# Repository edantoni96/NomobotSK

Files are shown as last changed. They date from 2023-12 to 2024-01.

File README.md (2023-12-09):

# NomobotSK

========== PCB DESIGN FOR NOMOBOT SK ==========

NomobotSK is a educational robot for kids to learn programming and robotics.

## TOP VIEW

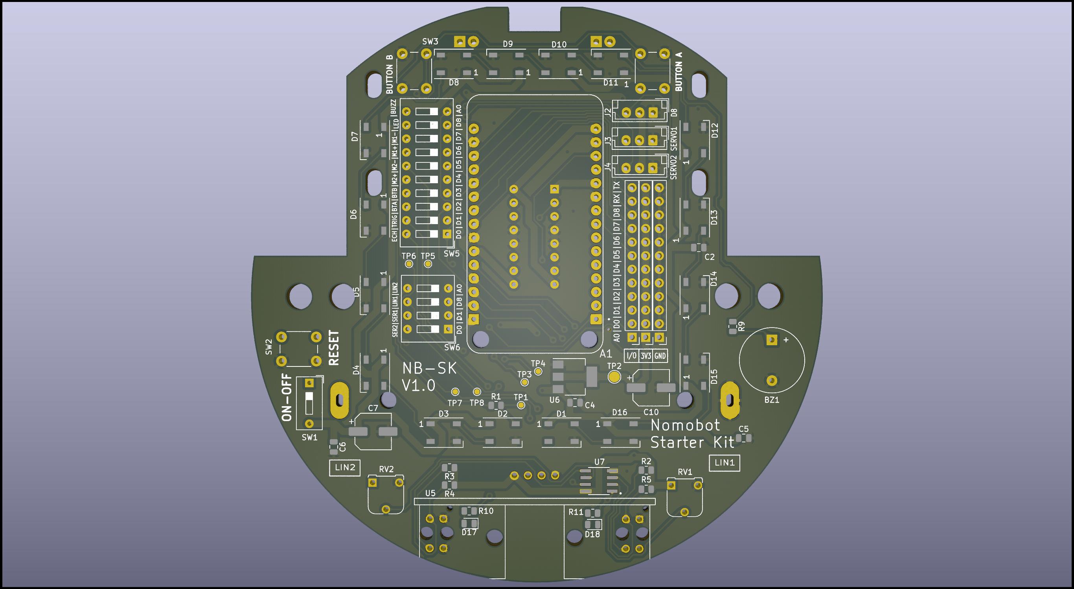
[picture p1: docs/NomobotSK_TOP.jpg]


## BOTTOM VIEW

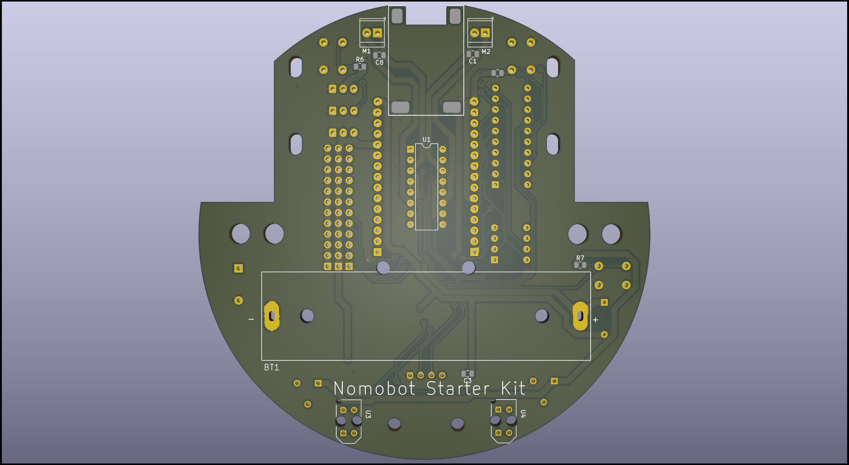
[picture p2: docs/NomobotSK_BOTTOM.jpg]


## SCHEMATIC

[embed](https://github.com/edantoni96/NomobotSK/blob/main/docs/schematic.pdf)

## TESTER

To test the device you can use the under tester/TEST.ino

\***\*KONFIGURASI PIN\*\***

D1; Trig / Servo R
D2; Tombol 2
D3; Tombol 3
D4; DIR2 (-)
D5; DIR2 (+)
D6; DIR1 (-)
D7; DIR1 (+)
D8; LED / Garis L
D0; BUZZ / Garis R

Catatan: Simbol / berarti setiap fungsi perlu diuji atau digunakan secara terpisah.

\***\*Perintah PENGUJIAN\*\***

1. TEST_LED
2. TEST_BUZ
3. TEST_BUTTON
4. TEST_M1
5. TEST_M2
6. TEST_ULRA
7. TEST_LINE

\***\*Instruksi Uji\*\***

1. Buka Test.ino dengan Arduino.
2. compile Test.ino.
3. Hubungkan NodeMCU Anda ke komputer menggunakan kabel USB.
4. Pilih board dan port yang sesuai di Arduino IDE.
5. Unggah kode yang telah dikompilasi ke NodeMCU dengan mengklik tombol "Unggah".
6. Setelah pengunggahan selesai, buka Serial Monitor di Arduino IDE.
7. TEST_LED
   - Nyalakan pin LED
   - Ketik "TEST_LED" di Serial Monitor dan tekan Enter.
   - Pastikan bahwa LED yang terhubung ke pin D8 (Garis L) menyala.
8. TEST_BUZ
   - Nyalakan pin Buzz
   - Ketik "TEST_BUZ" di Serial Monitor dan tekan Enter.
   - Konfirmasikan bahwa buzzer yang terhubung ke pin D0 (Garis R) menghasilkan suara.
9. TEST_BUTTON
   - Nyalakan BTA dan BTB
   - Ketik "TEST_BUTTON" di Serial Monitor dan tekan Enter.
   - Tekan Tombol 2 (terhubung ke pin D2) dan Tombol 3 (terhubung ke pin D3) satu per satu.
   - Amati di Serial Monitor bahwa tekanan tombol yang sesuai terdeteksi.
10. TEST_M1
    - Nyalakan pin M1+ dan M1-
    - Ketik "TEST_M1" di Serial Monitor dan tekan Enter.
    - Pastikan bahwa motor (M1) merespons sesuai dengan sinyal DIR1 (-) dan DIR1 (+) pada pin D6 dan D7.
11. TEST_M2
    - Nyalakan pin M2+ dan M2-
    - Ketik "TEST_M2" di Serial Monitor dan tekan Enter.
    - Pastikan bahwa motor (M2) merespons sesuai dengan sinyal DIR2 (-) dan DIR2 (+) pada pin D4 dan D5.
12. TEST_ULRA
    - Nyalakan pin Echo dan Trig
    - Ketik "TEST_ULRA" di Serial Monitor dan tekan Enter.
    - Jika sensor ultrasonik terhubung, periksa Serial Monitor untuk pembacaan jarak.
13. TEST_LINE
    - Nyalakan pin Garis
    - Ketik "TEST_LINE" di Serial Monitor dan tekan Enter.
    - Amati perilaku sensor garis yang terhubung ke pin D8 (Garis L) dan D0 (Garis R).
    - Pastikan pembacaan sensor tercermin di Serial Monitor.

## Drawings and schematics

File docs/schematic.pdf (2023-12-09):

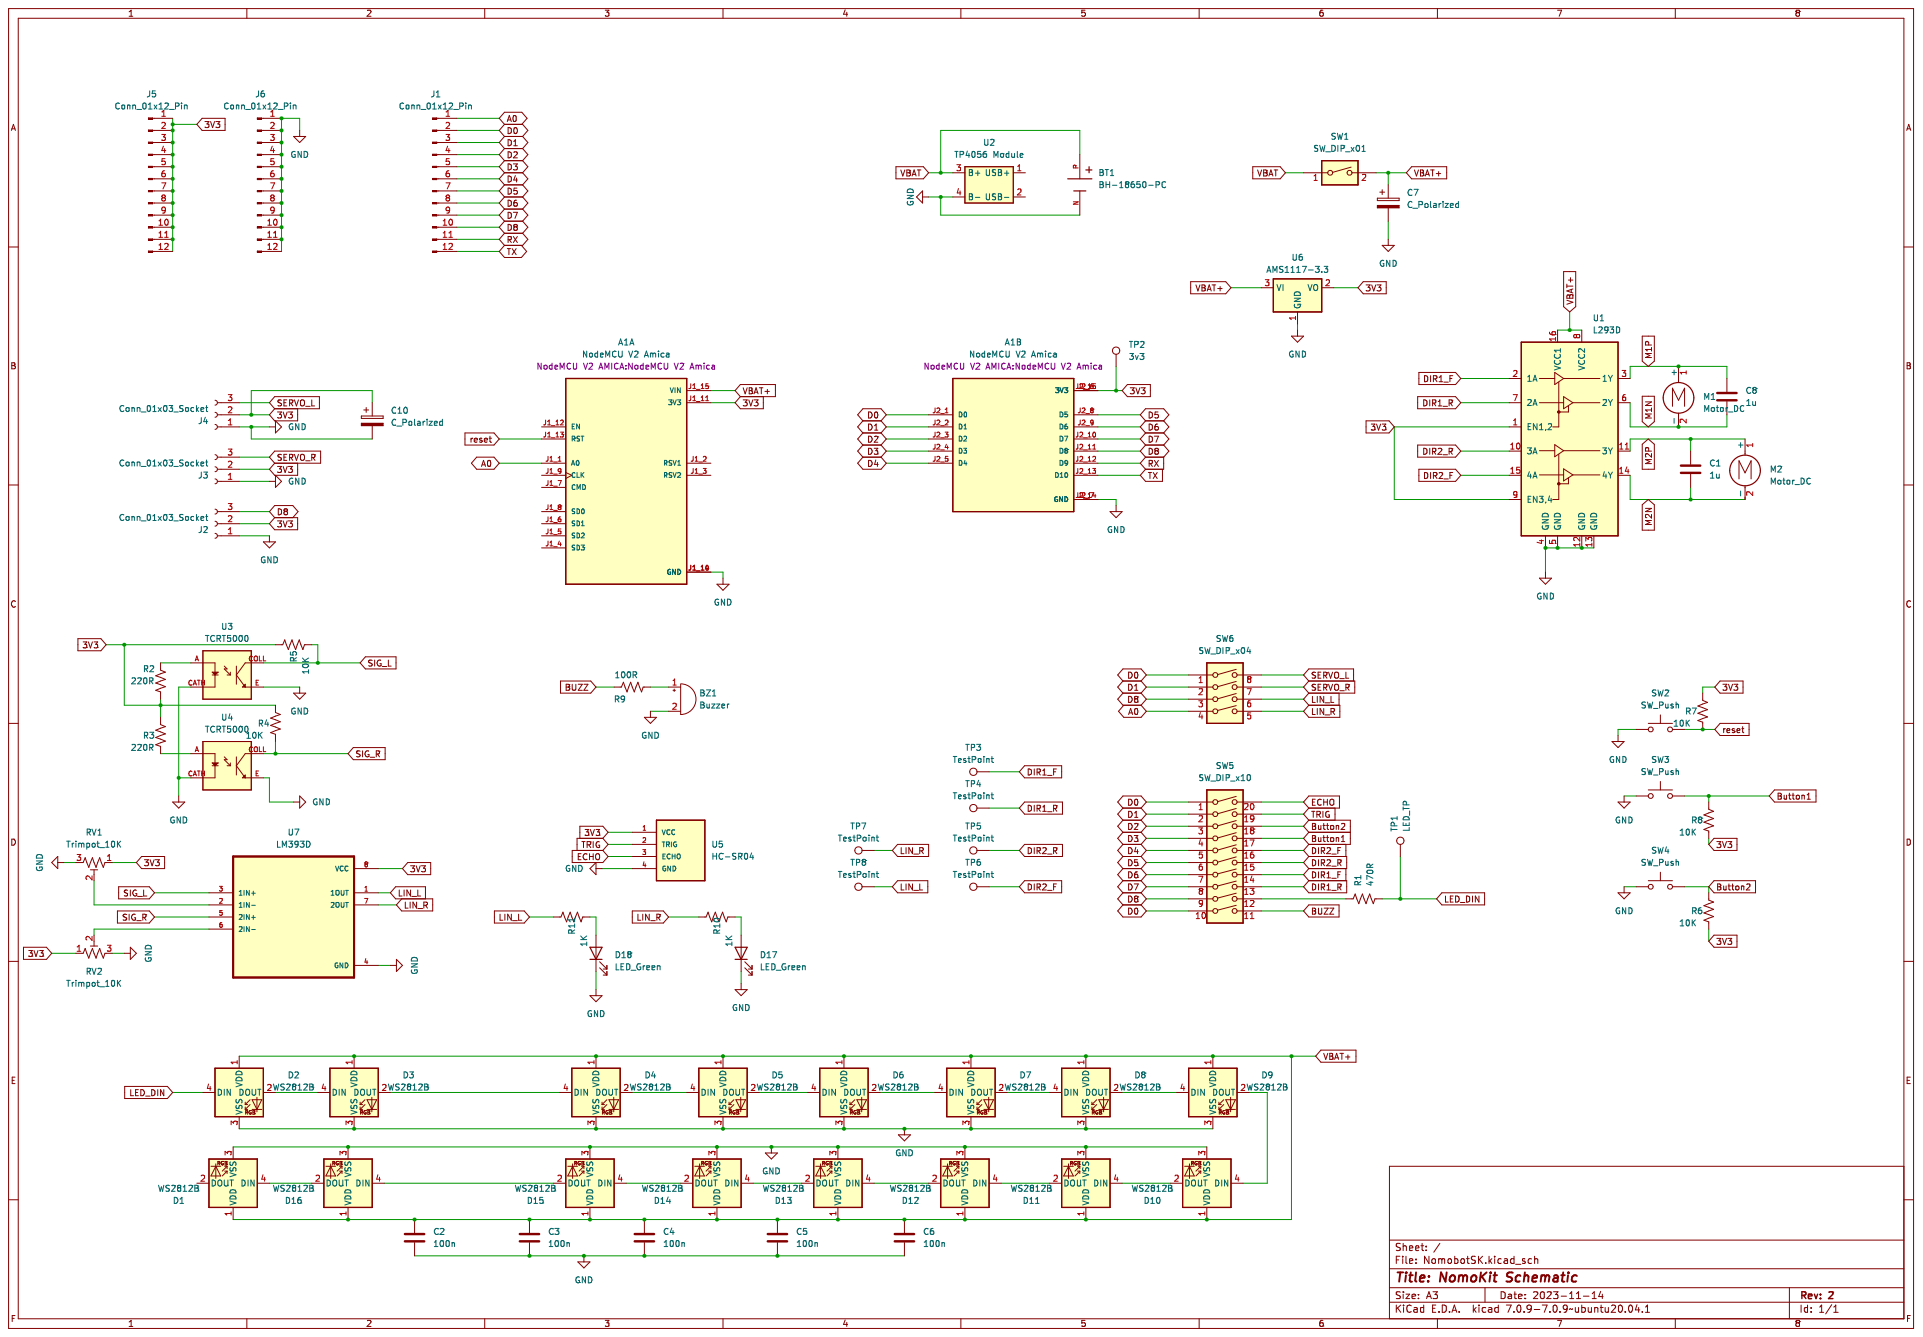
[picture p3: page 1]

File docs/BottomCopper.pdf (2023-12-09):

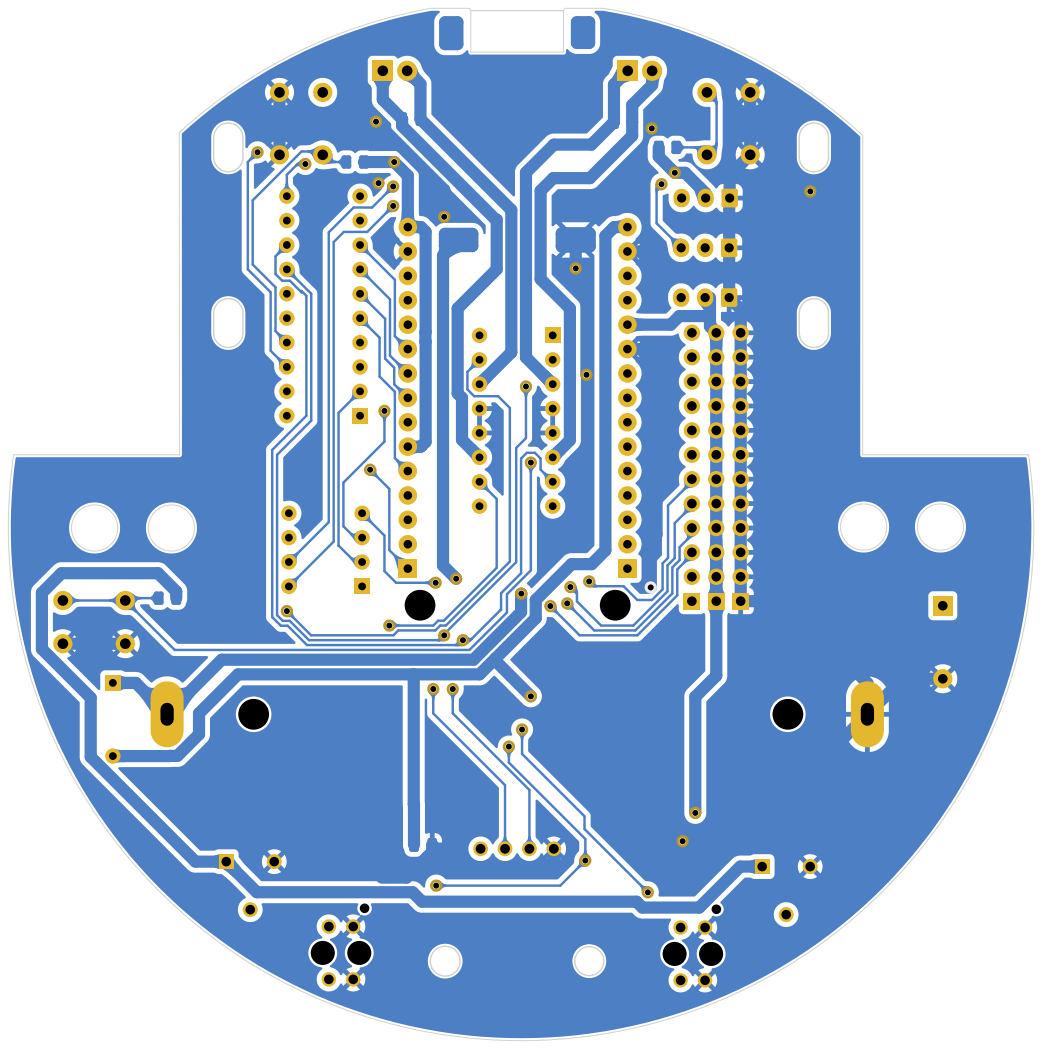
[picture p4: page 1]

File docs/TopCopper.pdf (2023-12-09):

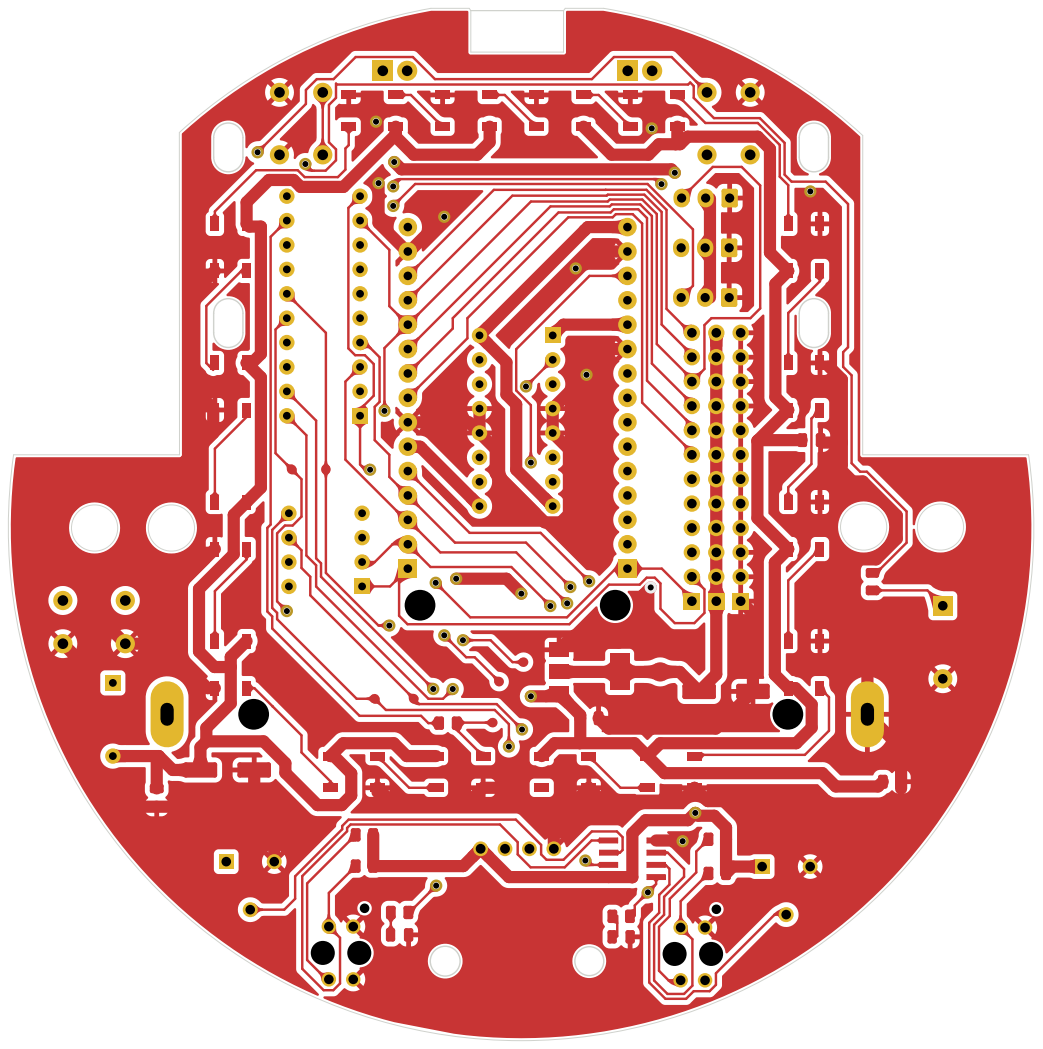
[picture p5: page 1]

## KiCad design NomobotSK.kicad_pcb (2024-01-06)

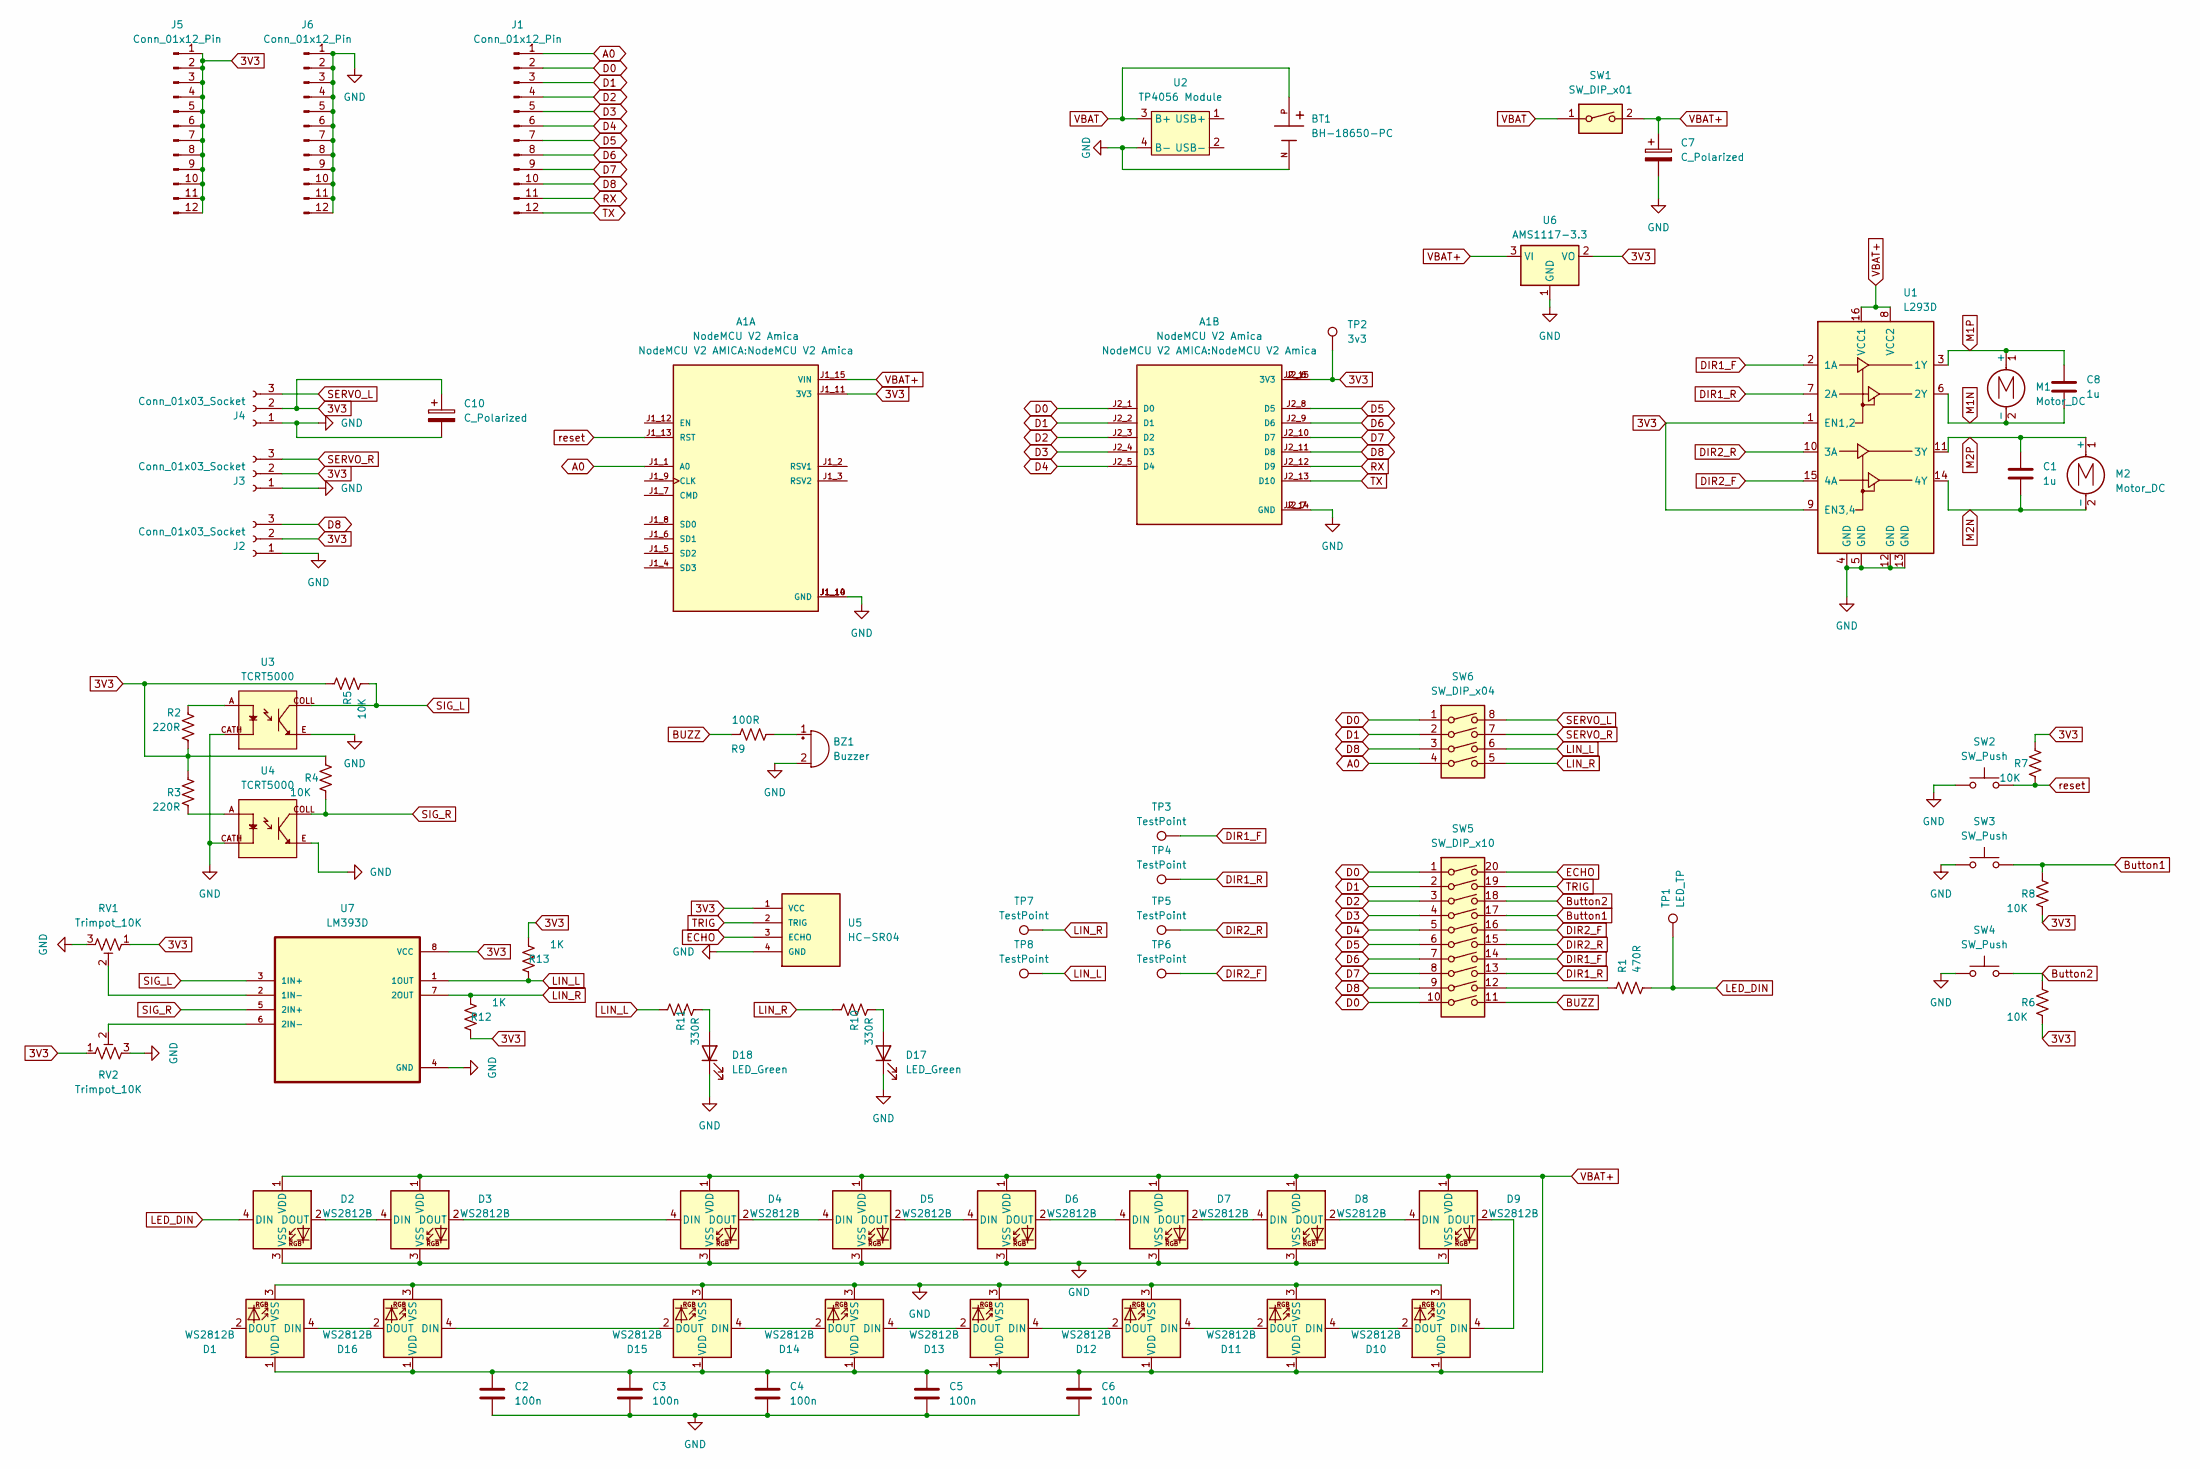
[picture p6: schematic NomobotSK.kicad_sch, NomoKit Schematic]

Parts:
A1: NodeMCU V2 Amica; PARTREV N/A
BT1: BH-18650-PC; BAT_BH-18650-PC; PARTREV 05/17/19
BZ1: Buzzer; Buzzer_12x9.5RM7.6
C1, C8: 1u; C_0805_2012Metric
C2, C3, C4, C5, C6: 100n; C_0805_2012Metric
C7, C10: C_Polarized; CP_Elec_6.3x5.3
D1, D2, D3, D4, D5, D6, D7, D8, D9, D10, D11, D12, D13, D14, D15, D16: WS2812B; LED_WS2812B_PLCC4_5.0x5.0mm_P3.2mm
D17, D18: LED_Green; LED_0805_2012Metric
J1, J5, J6: Conn_01x12_Pin; PinHeader_1x12_P2.54mm_Vertical
J2, J3, J4: Conn_01x03_Socket; JST_EH_B3B-EH-A_1x03_P2.50mm_Vertical
M1, M2: Motor_DC; TerminalBlock_TE_282834-2_1x02_P2.54mm_Horizontal
R1: 470R; R_0805_2012Metric
R2, R3: 220R; R_0805_2012Metric
R4, R5, R6, R7, R8: 10K; R_0805_2012Metric
R9: 100R; R_0805_2012Metric
R10, R11: 330R; R_0805_2012Metric
R12, R13: 1K; R_0805_2012Metric
RV1, RV2: Trimpot_10K; Potentiometer_Runtron_RM-065_Vertical
SW1: SW_DIP_x01; SW_DIP_SPSTx01_Slide_9.78x4.72mm_W7.62mm_P2.54mm
SW2, SW3, SW4: SW_Push; SW_PUSH_6mm_H4.3mm
SW5: SW_DIP_x10; SW_DIP_SPSTx10_Slide_9.78x27.58mm_W7.62mm_P2.54mm
SW6: SW_DIP_x04; SW_DIP_SPSTx04_Slide_9.78x12.34mm_W7.62mm_P2.54mm
TP1: LED_TP; TestPoint_Pad_D1.0mm
TP2: 3v3; TestPoint_Pad_D2.0mm
TP3, TP4, TP5, TP6, TP7, TP8: TestPoint; TestPoint_Pad_D1.0mm
U1: L293D; DIP-16_W7.62mm
U2: TP4056 Module; TP4056_Module
U3, U4: TCRT5000; OPTO_TCRT5000; PARTREV 1.7
U5: HC-SR04; XCVR_HC-SR04
U6: AMS1117-3.3; SOT-223-3_TabPin2
U7: LM393D; SOIC127P599X175-8N

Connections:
3V3: A1.J1_11 (3V3), A1.J2_6 (3V3), A1.J2_15 (3V3), C10.1, J2.2, J3.2, J4.2, J5.1, J5.2, J5.3, J5.4, J5.5, J5.6, J5.7, J5.8, J5.9, J5.10, J5.11, J5.12, R2.2, R3.1, R4.1, R5.1, R6.2, R7.1, R8.2, R12.1, R13.2, RV1.1, RV2.1, TP2.1, U1.1 (EN1,2), U1.9 (EN3,4), U5.1 (VCC), U6.2 (VO), U7.8 (VCC)
A0: A1.J1_1 (A0), J1.1, SW6.4
BUZZ: R9.1, SW5.11
Button1: R8.1, SW3.2, SW5.17
Button2: R6.1, SW4.2, SW5.18
D0: A1.J2_1 (D0), J1.2, SW5.1, SW5.10, SW6.1
D1: A1.J2_2 (D1), J1.3, SW5.2, SW6.2
D2: A1.J2_3 (D2), J1.4, SW5.3
D3: A1.J2_4 (D3), J1.5, SW5.4
D4: A1.J2_5 (D4), J1.6, SW5.5
D5: A1.J2_8 (D5), J1.7, SW5.6
D6: A1.J2_9 (D6), J1.8, SW5.7
D7: A1.J2_10 (D7), J1.9, SW5.8
D8: A1.J2_11 (D8), J1.10, J2.3, SW5.9, SW6.3
DIR1_F: SW5.14, TP3.1, U1.2 (1A)
DIR1_R: SW5.13, TP4.1, U1.7 (2A)
DIR2_F: SW5.16, TP6.1, U1.15 (4A)
DIR2_R: SW5.15, TP5.1, U1.10 (3A)
ECHO: SW5.20, U5.3 (ECHO)
GND: A1.J1_10 (GND), A1.J1_14 (GND), A1.J2_7 (GND), A1.J2_14 (GND), BT1.N, BZ1.2 (+), C2.2, C3.2, C4.2, C5.2, C6.2, C7.2, C10.2, D1.3 (VSS), D2.3 (VSS), D3.3 (VSS), D4.3 (VSS), D5.3 (VSS), D6.3 (VSS), D7.3 (VSS), D8.3 (VSS), D9.3 (VSS), D10.3 (VSS), D11.3 (VSS), D12.3 (VSS), D13.3 (VSS), D14.3 (VSS), D15.3 (VSS), D16.3 (VSS), D17.1 (K), D18.1 (K), J2.1, J3.1, J4.1, J6.1, J6.2, J6.3, J6.4, J6.5, J6.6, J6.7, J6.8, J6.9, J6.10, J6.11, J6.12, RV1.3, RV2.3, SW2.1, SW3.1, SW4.1, U1.4 (GND), U1.5 (GND), U1.12 (GND), U1.13 (GND), U2.4 (B-), U3.CATH, U3.E, U4.CATH, U4.E, U5.4 (GND), U6.1 (GND), U7.4 (GND)
LED_DIN: D2.4 (DIN), R1.2, TP1.1
LIN_L: R11.1, R13.1, SW6.6, TP8.1, U7.1 (1OUT)
LIN_R: R10.1, R12.2, SW6.5, TP7.1, U7.7 (2OUT)
M1N: C8.2, M1.2 (-), U1.6 (2Y)
M1P: C8.1, M1.1 (+), U1.3 (1Y)
M2N: C1.2, M2.2 (-), U1.14 (4Y)
M2P: C1.1, M2.1 (+), U1.11 (3Y)
unnamed: BZ1.1 (-), R9.2
unnamed: D1.4 (DIN), D16.2 (DOUT)
unnamed: D2.2 (DOUT), D3.4 (DIN)
unnamed: D3.2 (DOUT), D4.4 (DIN)
unnamed: D4.2 (DOUT), D5.4 (DIN)
unnamed: D5.2 (DOUT), D6.4 (DIN)
unnamed: D6.2 (DOUT), D7.4 (DIN)
unnamed: D7.2 (DOUT), D8.4 (DIN)
unnamed: D8.2 (DOUT), D9.4 (DIN)
unnamed: D9.2 (DOUT), D10.4 (DIN)
unnamed: D10.2 (DOUT), D11.4 (DIN)
unnamed: D11.2 (DOUT), D12.4 (DIN)
unnamed: D12.2 (DOUT), D13.4 (DIN)
unnamed: D13.2 (DOUT), D14.4 (DIN)
unnamed: D14.2 (DOUT), D15.4 (DIN)
unnamed: D15.2 (DOUT), D16.4 (DIN)
unnamed: D17.2 (A), R10.2
unnamed: D18.2 (A), R11.2
unnamed: R1.1, SW5.12
unnamed: R2.1, U3.A
unnamed: R3.2, U4.A
unnamed: RV1.2, U7.2 (1IN-)
unnamed: RV2.2, U7.6 (2IN-)
RX: A1.J2_12 (D9), J1.11
SERVO_L: J4.3, SW6.8
SERVO_R: J3.3, SW6.7
SIG_L: R5.2, U3.COLL, U7.3 (1IN+)
SIG_R: R4.2, U4.COLL, U7.5 (2IN+)
TRIG: SW5.19, U5.2 (TRIG)
TX: A1.J2_13 (D10), J1.12
VBAT: BT1.P, SW1.1, U2.3 (B+)
VBAT+: A1.J1_15 (VIN), C2.1, C3.1, C4.1, C5.1, C6.1, C7.1, D1.1 (VDD), D2.1 (VDD), D3.1 (VDD), D4.1 (VDD), D5.1 (VDD), D6.1 (VDD), D7.1 (VDD), D8.1 (VDD), D9.1 (VDD), D10.1 (VDD), D11.1 (VDD), D12.1 (VDD), D13.1 (VDD), D14.1 (VDD), D15.1 (VDD), D16.1 (VDD), SW1.2, U1.8 (VCC2), U1.16 (VCC1), U6.3 (VI)
reset: A1.J1_13 (RST), R7.2, SW2.2

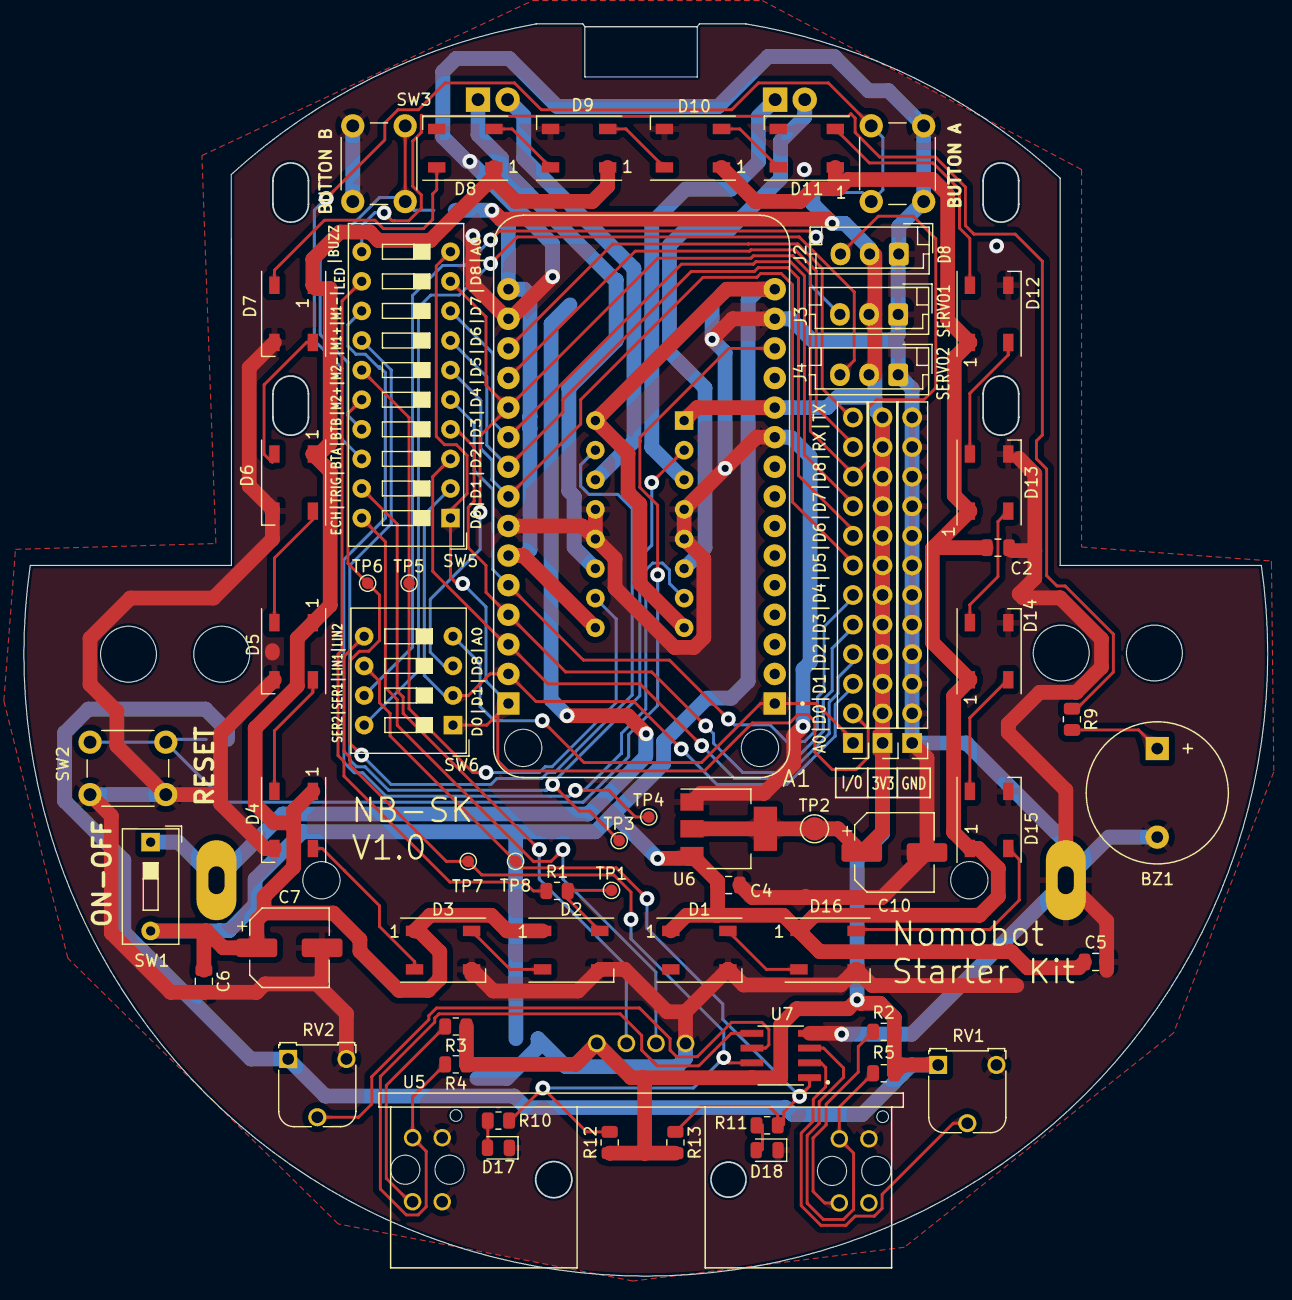
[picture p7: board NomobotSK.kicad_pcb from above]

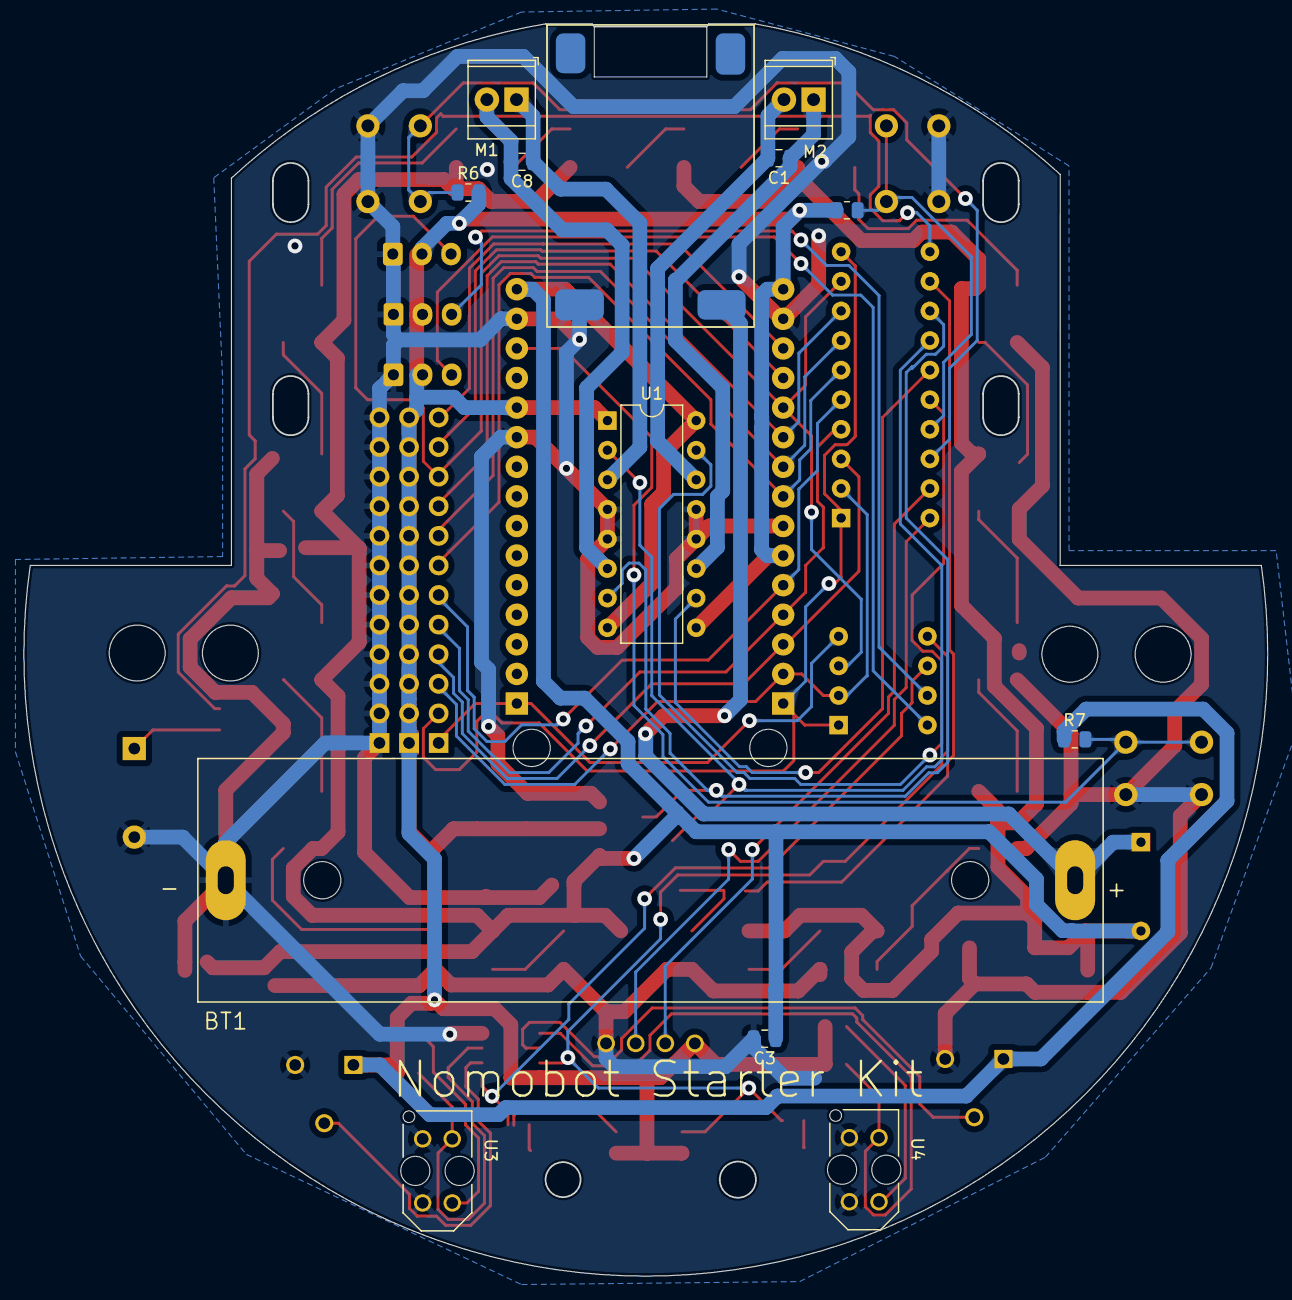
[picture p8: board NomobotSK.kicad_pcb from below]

Board: 2 copper layers, 106.8 x 107.5 mm, 74 parts (13 on the bottom side), 60 nets.

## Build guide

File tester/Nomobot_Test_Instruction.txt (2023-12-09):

****PIN CONFIGURATION****

D1; Trig / Servo R
D2; Button 2
D3; Button 3
D4; DIR2 (-)
D5; DIR2 (+)
D6; DIR1 (-)
D7; DIR1 (+)
D8; LED / Line L
D0; BUZZ / Line R

Note: / symbol means each of the function need to be tested or used separately.

****TEST Command****

1. TEST_LED
2. TEST_BUZ
3. TEST_BUTTON
4. TEST_M1
5. TEST_M2
6. TEST_ULRA
7. TEST_LINE

****Test Instruction****

1. Open Test.ino with Arduino.
2. Compile Test.ino.
3. Connect your NodeMCU to your computer using a USB cable.
4. Select the appropriate board and port in the Arduino IDE.
5. Upload the compiled code to the NodeMCU by clicking the "Upload" button.
6. Once the upload is complete, open the Serial Monitor in the Arduino IDE.
7. TEST_LED
	- Switch on Led Pin
	- Type "TEST_LED" in the Serial Monitor and press Enter.
	- Verify that the LED connected to pin D8 (Line L) turns on.
8. TEST_BUZ
	- Switch on Buz Pin
	- Type "TEST_BUZ" in the Serial Monitor and press Enter.
	- Confirm that the buzzer connected to pin D0 (Line R) produces a sound.
9. TEST_BUTTON
	- Switch on Button A and B Pins
	- Type "TEST_BUTTON" in the Serial Monitor and press Enter.
	- Press Button 2 (connected to pin D2) and Button 3 (connected to pin D3) one by one.
	- Observe in the Serial Monitor that the corresponding button presses are detected.
10. TEST_M1
	- Switch on M1 pins
	- Type "TEST_M1" in the Serial Monitor and press Enter.
	- Confirm that the motor (M1) responds accordingly based on the DIR1 (-) and DIR1 (+) 		signals on pins D6 and D7.
11. TEST_M2
	- Switch on M2 Pins
	- Type "TEST_M2" in the Serial Monitor and press Enter.
	- Confirm that the motor (M2) responds accordingly based on the DIR2 (-) and DIR2 (+) 		signals on pins D4 and D5.
12. TEST_ULRA
	- Switch on Echo and Trig Pins
	- Type "TEST_ULRA" in the Serial Monitor and press Enter.
	- If an ultrasonic sensor is connected, check the Serial Monitor for the distance 		readings.
13. TEST_LINE
	- Switch on Lin Pins
	- Type "TEST_LINE" in the Serial Monitor and press Enter.
	- Observe the behavior of the line sensors connected to pins D8 (Line L) and D0 (Line 		R).
	- Verify that the sensor readings are reflected in the Serial Monitor.
	
Note: Ensure that you have the necessary libraries, dependencies, and hardware connections set up correctly for each test. Adjust the pin configurations and commands as needed based on your actual hardware setup.

****KONFIGURASI PIN****

D1; Trig / Servo R
D2; Tombol 2
D3; Tombol 3
D4; DIR2 (-)
D5; DIR2 (+)
D6; DIR1 (-)
D7; DIR1 (+)
D8; LED / Garis L
D0; BUZZ / Garis R

Catatan: Simbol / berarti setiap fungsi perlu diuji atau digunakan secara terpisah.

****Perintah PENGUJIAN****

1. TEST_LED
2. TEST_BUZ
3. TEST_BUTTON
4. TEST_M1
5. TEST_M2
6. TEST_ULRA
7. TEST_LINE

****Instruksi Uji****

1. Buka Test.ino dengan Arduino.
2. compile Test.ino.
3. Hubungkan NodeMCU Anda ke komputer menggunakan kabel USB.
4. Pilih board dan port yang sesuai di Arduino IDE.
5. Unggah kode yang telah dikompilasi ke NodeMCU dengan mengklik tombol "Unggah".
6. Setelah pengunggahan selesai, buka Serial Monitor di Arduino IDE.
7. TEST_LED
	- Nyalakan pin LED
	- Ketik "TEST_LED" di Serial Monitor dan tekan Enter.
	- Pastikan bahwa LED yang terhubung ke pin D8 (Garis L) menyala.
8. TEST_BUZ
	- Nyalakan pin Buz
	- Ketik "TEST_BUZ" di Serial Monitor dan tekan Enter.
	- Konfirmasikan bahwa buzzer yang terhubung ke pin D0 (Garis R) menghasilkan suara.
9. TEST_BUTTON
	- Nyalakan Tombol A dan Tombol B
	- Ketik "TEST_BUTTON" di Serial Monitor dan tekan Enter.
	- Tekan Tombol 2 (terhubung ke pin D2) dan Tombol 3 (terhubung ke pin D3) satu per 		satu.
	- Amati di Serial Monitor bahwa tekanan tombol yang sesuai terdeteksi.
10. TEST_M1
	- Nyalakan pin M1
	- Ketik "TEST_M1" di Serial Monitor dan tekan Enter.
	- Pastikan bahwa motor (M1) merespons sesuai dengan sinyal DIR1 (-) dan DIR1 (+) pada 		pin D6 dan D7.
11. TEST_M2
	- Nyalakan pin M2
	- Ketik "TEST_M2" di Serial Monitor dan tekan Enter.
	- Pastikan bahwa motor (M2) merespons sesuai dengan sinyal DIR2 (-) dan DIR2 (+) pada 		pin D4 dan D5.
12. TEST_ULRA
	- Nyalakan pin Echo dan Trig
	- Ketik "TEST_ULRA" di Serial Monitor dan tekan Enter.
	- Jika sensor ultrasonik terhubung, periksa Serial Monitor untuk pembacaan jarak.
13. TEST_LINE
	- Nyalakan pin Garis
	- Ketik "TEST_LINE" di Serial Monitor dan tekan Enter.
	- Amati perilaku sensor garis yang terhubung ke pin D8 (Garis L) dan D0 (Garis R).
	- Pastikan pembacaan sensor tercermin di Serial Monitor.

Catatan: Pastikan Anda memiliki library, dependensi, dan koneksi perangkat keras yang diperlukan dengan benar untuk setiap uji. Sesuaikan konfigurasi pin dan perintah sesuai dengan pengaturan perangkat keras sebenarnya Anda.

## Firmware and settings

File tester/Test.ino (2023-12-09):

#include <Adafruit_NeoPixel.h>

String input;

static const uint8_t echo = D0;
static const uint8_t trigger = D1;
static const uint8_t servo_l = D0;
static const uint8_t servo_r = D1;
static const uint8_t button_A = D2;
static const uint8_t button_B = D3;
static const uint8_t motor_2n = D4;
static const uint8_t motor_2p = D5;
static const uint8_t motor_1n = D6;
static const uint8_t motor_1p = D7;
static const uint8_t led_pin = D8;
static const uint8_t buzz_pin = D0 ;
static const uint8_t line_l = D8;
static const uint8_t line_r = A0;

Adafruit_NeoPixel pixels = Adafruit_NeoPixel(16, D8, NEO_GRB + NEO_KHZ800);


void setup() {
  Serial.begin(115200);
  pinMode(motor_2n, OUTPUT);
  pinMode(motor_2p, OUTPUT);
  pinMode(motor_1n, OUTPUT);
  pinMode(motor_1p, OUTPUT);
  pinMode(led_pin, OUTPUT);
  pinMode(button_A, INPUT);
  pinMode(button_B, INPUT);
  pinMode(line_r, INPUT);
  pixels.begin();
  setColor(0,255,255,255,100);
}

// the loop function runs over and over again forever
void loop() {
  Serial.println("TEST PROGRAM");

  while(!Serial.available())
  {
  }

  input = Serial.readString();
  Serial.println(input);

  if(input == "TEST_M1\n") {
    Serial.println("Test Motor DC 1 Forward");
    digitalWrite(motor_1p, HIGH);
    digitalWrite(motor_1n, LOW);
    delay(5000);
    digitalWrite(motor_1p, LOW);
    digitalWrite(motor_1n, LOW);
    delay(1000);
    Serial.println("Test Motor DC 1 Backward");
    digitalWrite(motor_1p, LOW);
    digitalWrite(motor_1n, HIGH);
    delay(5000);
    Serial.println("Test Motor DC 1 Stop");
    digitalWrite(motor_1p, LOW);
    digitalWrite(motor_1n, LOW);
  }
  else if(input == "TEST_M2\n") {
    Serial.println("Test Motor DC 2 Forward");
    digitalWrite(motor_2p, HIGH);
    digitalWrite(motor_2n, LOW);
    delay(5000);
    digitalWrite(motor_2p, LOW);
    digitalWrite(motor_2n, LOW);
    delay(1000);
    Serial.println("Test Motor DC 2 Backward");
    digitalWrite(motor_2p, LOW);
    digitalWrite(motor_2n, HIGH);
    delay(5000);
    Serial.println("Test Motor DC 2 Stop");
    digitalWrite(motor_2p, LOW);
    digitalWrite(motor_2n, LOW);
  }
  else if(input == "TEST_LED\n") {
    Serial.println("Test Led");
    int led = 0;
    for(led=0; led <16; led++)
    {
      setColor(led,255,0,0,100); //red
    }
    for(led=0; led <16; led++)
    {
      setColor(led,0,255,0,100);
    }
    for(led=0; led <16; led++)
    {
      setColor(led,0,0,255,100); 
    }
  }
  else if(input == "TEST_BUZ\n") {
    pinMode(buzz_pin, OUTPUT);
    Serial.println("Test Buzzer");
    delay(500);
    digitalWrite(buzz_pin, HIGH);
    delay(500);
    digitalWrite(buzz_pin, LOW);
    delay(1000);
    digitalWrite(buzz_pin, HIGH);
    delay(500);
    digitalWrite(buzz_pin, LOW);
    delay(1000);
    digitalWrite(buzz_pin, HIGH);
    delay(500);
    digitalWrite(buzz_pin, LOW);
    Serial.println("Test Buzzer Done");
  }
  else if(input == "TEST_ULTRA\n") {
    String data, command;
    long duration;
    int distance;
    pinMode(trigger, OUTPUT);
    pinMode(echo, INPUT);
    Serial.println("Test Ultrasonic");
    while(1){
      if(Serial.available()){
        command = Serial.readString();
        if(command == "STOP\n") {
          break;
        }
      }
      digitalWrite(trigger, LOW);
      delayMicroseconds(2);
      // Sets the trigPin on HIGH state for 10 micro seconds
      digitalWrite(trigger, HIGH);
      delayMicroseconds(10);
      digitalWrite(trigger, LOW);
      // Reads the echoPin, returns the sound wave travel time in microseconds
      duration = pulseIn(echo, HIGH);
      // Calculating the distance
      distance = duration * 0.034 / 2;
      // Prints the distance on the Serial Monitor
      Serial.print("Distance: ");
      Serial.println(distance);
      delay(200);
    }
  }
  else if(input == "TEST_LINE\n") {
    int lstat,rstat;
    String command;
    pinMode(line_l, INPUT);
    pinMode(line_r, INPUT);

    while (1) {
      if(Serial.available()){
        command = Serial.readString();
        if(command == "STOP\n") {
          break;
        }
      }
      lstat = digitalRead(line_l);
      rstat = analogRead(line_r);
      Serial.print("right : ");
      Serial.print(rstat);
      Serial.print(" | left : ");
      Serial.println(lstat);
    }
  }
  else if (input == "TEST_BUTTON\n"){
    String command;
    while(1) {
      if(!digitalRead(button_A)) {
        Serial.println("Button A pressed");
      }
      if(!digitalRead(button_B)) {
        Serial.println("Button B pressed");
      }
      if(Serial.available()){
        command = Serial.readString();
        if(command == "STOP\n") {
          break;
        }
      }
      delay(200);
    }
  }
  
}

void setColor(int led, int redValue, int greenValue, int blueValue, int delayValue)
{
  pixels.setPixelColor(led, pixels.Color(redValue, greenValue, blueValue)); 
  pixels.show();
  delay(delayValue);
}

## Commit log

2023-12-09 v1 push
    [NomobotSK.kicad_pcb, NomobotSK.kicad_sch]
2024-01-06 change design of comparator
    [NomobotSK.kicad_pcb, NomobotSK.kicad_sch]
